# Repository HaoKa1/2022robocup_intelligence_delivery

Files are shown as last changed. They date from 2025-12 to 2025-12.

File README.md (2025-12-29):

# 前言
22年赛道第一次设立，通宵达旦干了两个月，最后获得了冠军，三年过去了，忽然找到留存的资料，想起有好几个赛事群内的群友问我要过资料。虽赛事要求已发生了变化，但基本功能和逻辑一致，于是想直接开源出来，希望能帮助到参赛的同学，也希望赛事能得到更好的发展！  
时间久远，有些文件可能会有错误，欢迎指正，如果内容对你有用的话，请给个小星星⭐️！
# 介绍
PCB硬件设计部分由[@HaoKa1](https://github.com/HaoKa1)完成  
STM32控制代码部分由[@HaoKa1](https://github.com/HaoKa1)/Kaicheng Jin共同完成  
建模由[@hallice](https://github.com/hallice)/[@cdwisaxiaobai](https://github.com/cdwisaxiaobai)共同完成  
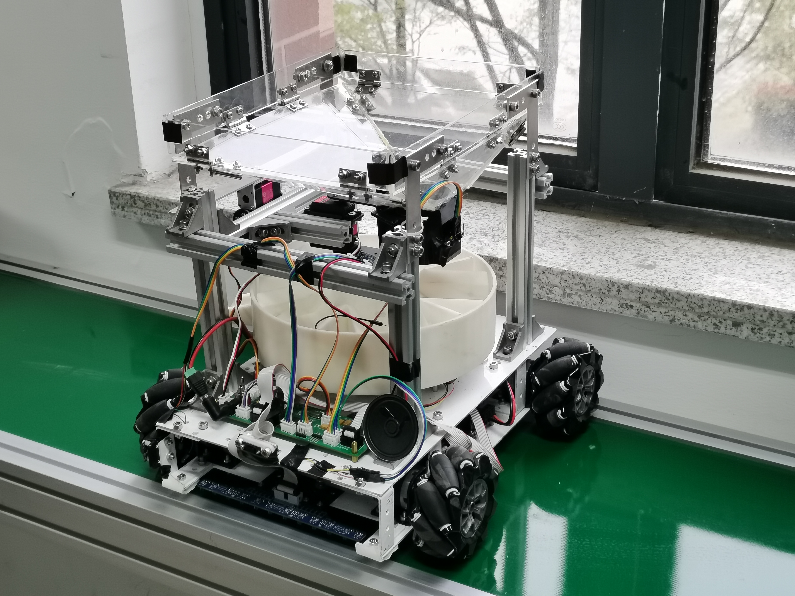
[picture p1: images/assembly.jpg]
Assembly Image

## 建模
结构使用亚克力板、铝合金板材和铝型材搭建，参考models目录下的文件
## 硬件
主控芯片选型为STM32F103RCT6，PCB元器件选型参考hardware目录下的工程文件，外设元器件参考如下，其中因主控芯片定时器数量限制，超声波测距实际上并未被使用                 
### 📡 传感模块
| 传感器类型 | 型号 | 功能 |
|:---|:-----|:-----|
| 激光测距 | ATK-MS53L0M | 距离判断 |
| 超声波测距 | HC-SR04 | 测量距离 |
| 灰度传感器 | 得科技术 | 循迹检测 |
| 颜色识别 | TCS3472XFN | 高尔夫球颜色识别 |

### 🚀 动力模块
| 部件类型 | 型号 | 功能 |
|:---|:-----|:-----|
| 电机驱动 | 得科技术 | 控制电机 |
| 电机 | 任意 | 驱动麦轮 |
| 麦轮 | 任意 | / |
| 舵机 | DS3220/DS3230 | 拨盘、转盘、开门 |

### 🎛️ 其他模块
| 模块类型 | 型号 | 功能 |
|:---|:-----|:-----|
| 扫码模块 | MG65 | 识别二维码 |
| 语音播报模块 | SYN 6288 | 播报信息 |

## 软件
单片机移植FreeRTOS做状态调度，简化调度逻辑，具体流程如下
```mermaid
graph TD
    %% 初始化部分
    Servo_Rest["Servo Rest()<br/>优先级: 2"] -->|挂起相关任务| Start["Start()<br/>优先级: 2"]
    Start -->|判断出发区| GoLine["GoLine()<br/>优先级: 1"]
    
    %% 主巡线循环
    GoLine -->|巡线中| TOF["TOF()<br/>优先级: 2"]
    GoLine -->|转弯信号| Corner["Corner()<br/>优先级: 2"]
    GoLine -->|接收测距通知| Stop["Stop()<br/>优先级: 1"]
    GoLine -->|超声波信号| Wave["Wave()<br/>优先级: 1"]
    
    %% 分选系统（优先级1）
    subgraph "分选系统 - 优先级1"
        Drop["Drop()<br/>1. 接受Stop信号<br/>2. 接受Judge/Select信号<br/>3. 转动<br/>4. 信号给Recognition"]
        Recognition["Recognition()<br/>1. 接受Drop信号<br/>2. 颜色存入队列HC<br/>3. 信号给Judge"]
        Judge["Judge()<br/>1. 接受Recognition信号<br/>2. 颜色判断<br/>3. 无球→JudgetoDrop<br/>4. 有球→颜色存入Index<br/>5. 信号给Select"]
        Select["Select()<br/>1. 接受Judge信号<br/>2. 从Index取颜色<br/>3. 转到对应位置<br/>4. 信号给Drop"]
        
        Drop -->|信号量D| Recognition
        Recognition -->|信号量Recognition| Judge
        Judge -->|无球: JudgetoDrop| Drop
        Judge -->|有球: 存入队列Index| Select
        Select -->|SelecttoDrop| Drop
    end
    
    %% 避障系统
    Wave -->|距离<250| Avoid["Avoid()<br/>优先级: 2"]
    Wave -->|>=250| GoLine
    Avoid -->|结束条件| GoLine
    
    %% 停车处理流程
    TOF -->|测距数据| Stop
    Stop -->|第一次停车| GoLineLow["挂起Goline<br/>拉起GolineLow"]
    Stop -->|通知Drop| Drop_Start["分选开始"]
    Stop -->|第2-7次停车| Movein["Movein()<br/>优先级: 1"]
    Stop -->|第8次停车| SlowCross["减速过跷跷板"]
    
    %% 货站操作流程
    Movein -->|右侧平移| QR["QR()<br/>优先级: 2"]
    QR -->|数据=0| Speak_0["Speak()<br/>播报0<br/>优先级: 3"]
    QR -->|数据≠0| Put["Put()<br/>优先级: 1"]
    
    QR -->|QRtoMoveout| Moveout["Moveout()<br/>优先级: 1"]
    Speak_0 -->|播报完成| Moveout
    Put -->|PuttoSpeak| Speak_1["Speak()<br/>播报颜色<br/>优先级: 3"]
    Put -->|PuttoMoveout| Moveout
    Speak_1 -->|播报完成| Moveout
    
    %% 继续前进
    Moveout -->|MoveouttoForward| Forward["Forward()<br/>优先级: 1"]
    Stop -->|20秒后| Forward_Continue["拉起Goline/相关任务"]
    Forward -->|拉起TOF/Goline/Stop/QR| GoLine
    
    %% 特殊流程
    Stop -->|第7次后| EnableFrontTOF["开启前方测距"]
    Corner -->|第4次转弯| ReturnStart["返回出发区"]
    
    %% 结束条件
    Judge -->|10个球分选完| DeleteModules["删除Drop/Recognition/Judge/Select"]
    ReturnStart --> End["流程结束"]

    %% 样式定义
    classDef priority1 fill:#e1f5fe,stroke:#0288d1,stroke-width:2px
    classDef priority2 fill:#f3e5f5,stroke:#7b1fa2,stroke-width:2px
    classDef priority3 fill:#e8f5e8,stroke:#2e7d32,stroke-width:2px
    classDef special fill:#fff3e0,stroke:#ef6c00,stroke-width:2px
    
    class Drop,Recognition,Judge,Select,GoLine,Stop,Movein,Put,Moveout,Forward,Wave priority1
    class Servo_Rest,Start,Corner,TOF,QR,Avoid priority2
    class Speak_0,Speak_1 priority3
    class DeleteModules,ReturnStart,EnableFrontTOF,SlowCross special
```

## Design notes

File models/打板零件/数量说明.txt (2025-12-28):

漏斗——1个
底板钣金——1个
横梁钣金——1个
底盘上板——1个
激光测距——2个
底盘_筛分连接——3个
镜像底盘_筛分连接——3个
平面直角连接——4个
转盘固定——4个

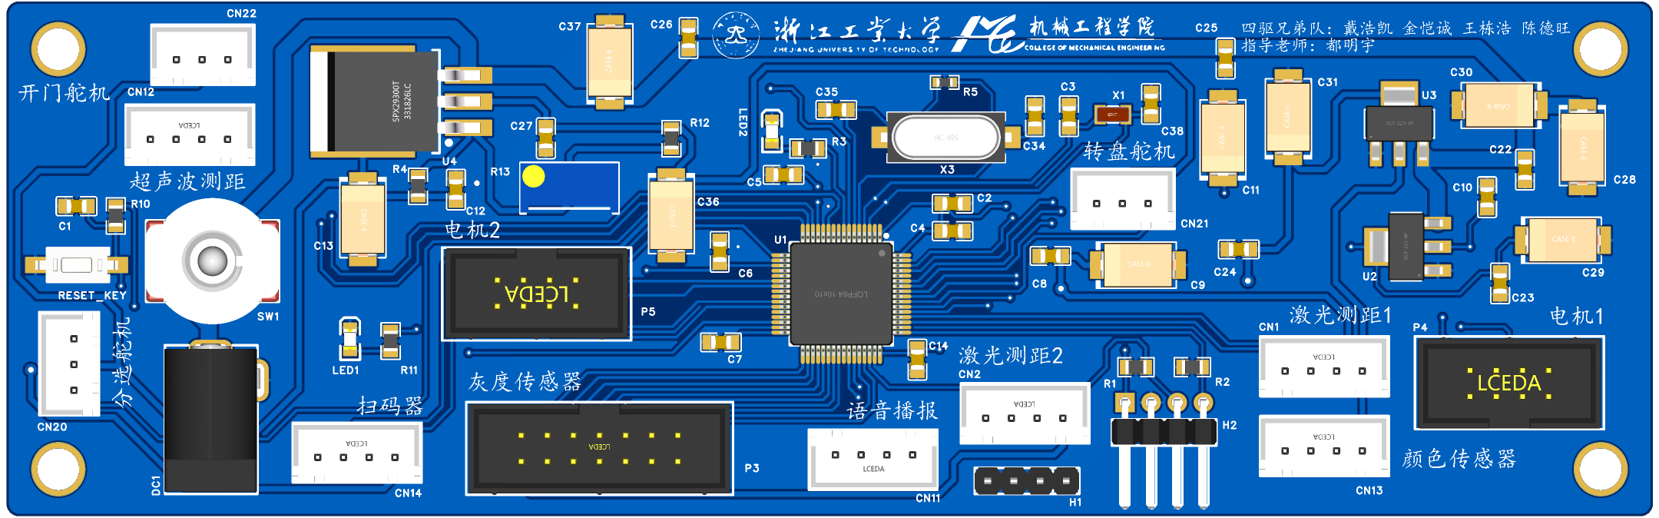
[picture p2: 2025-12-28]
hardware/3D_PCB.png

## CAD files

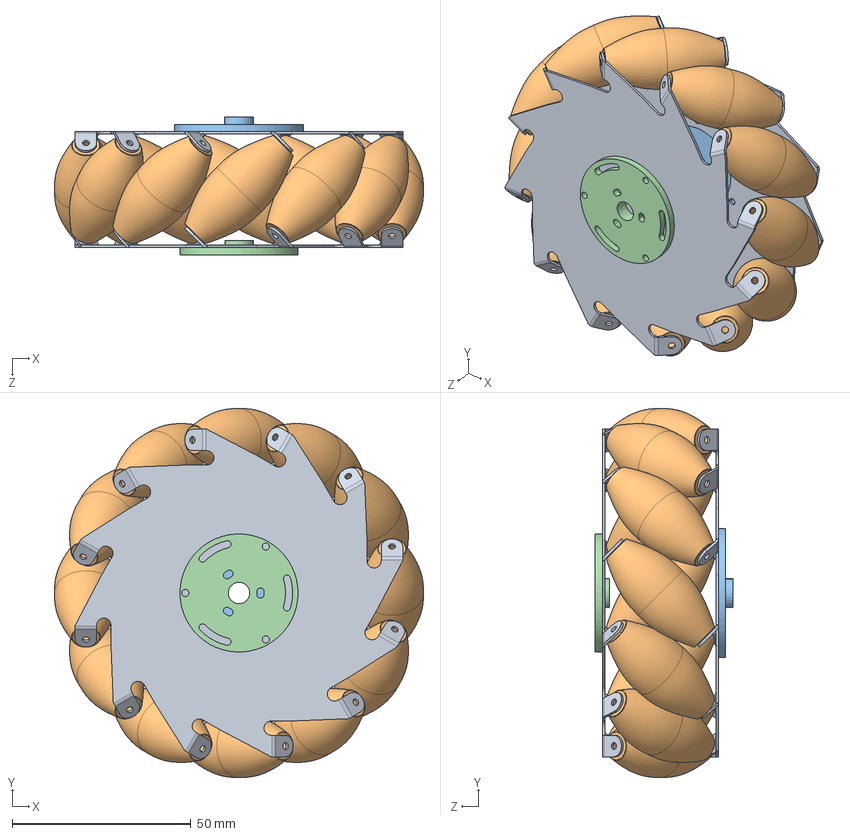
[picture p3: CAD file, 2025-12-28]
models/麦轮/麦轮.SLDASM
103.1 x 103.1 x 38.5 mm
麦轮轮毂 x 2
麦轮麦粒 x 12
轮毂配件
轮毂配件外

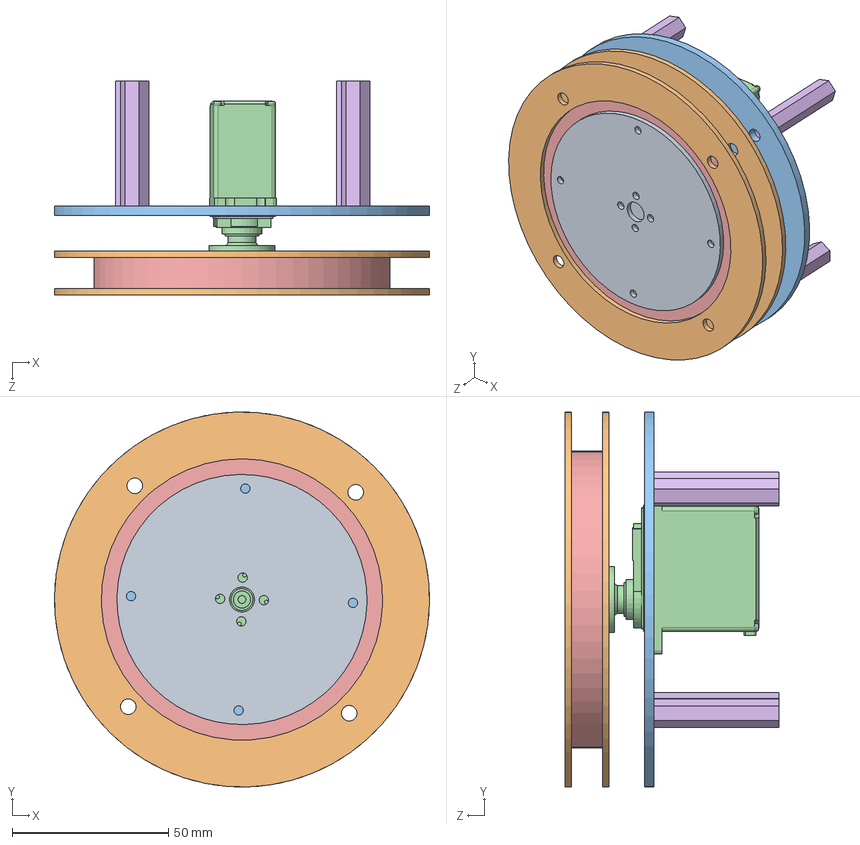
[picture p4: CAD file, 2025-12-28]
models/转盘/转盘.SLDASM
120.0 x 119.9 x 68.4 mm
上板 x 2
转盘轴承夹板 x 2
转盘底板
儋州舵机
轴承
铜柱 x 4

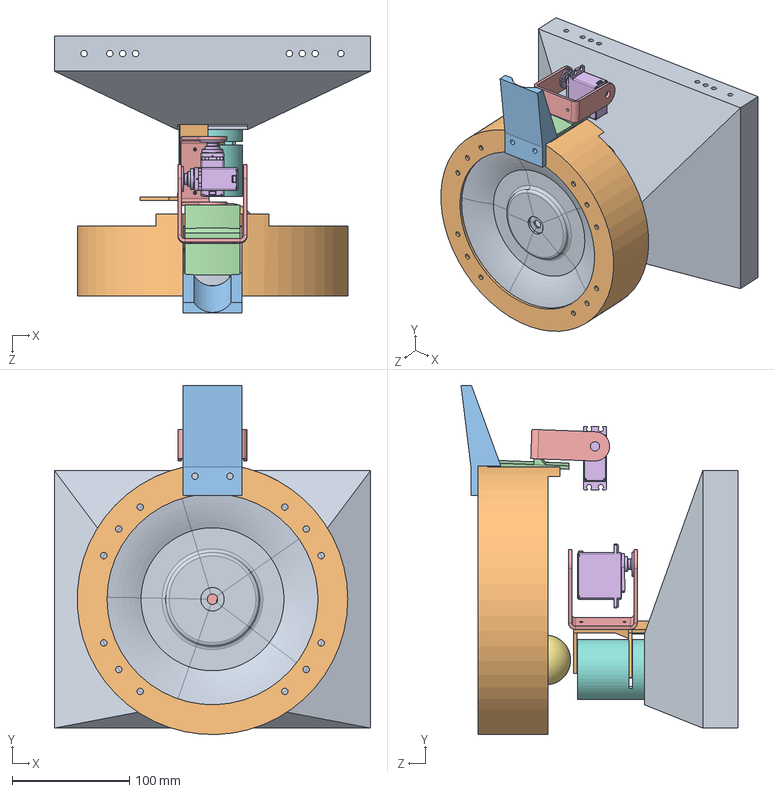
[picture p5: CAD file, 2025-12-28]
models/储存模块2.0/装配体2.SLDASM
270.0 x 297.9 x 236.5 mm
筛选器 x 5
遮挡
滑槽
挡板1
舵机架 x 2
儋州舵机 x 2
高尔夫球 x 4
圆筒
漏斗
遮挡转轴

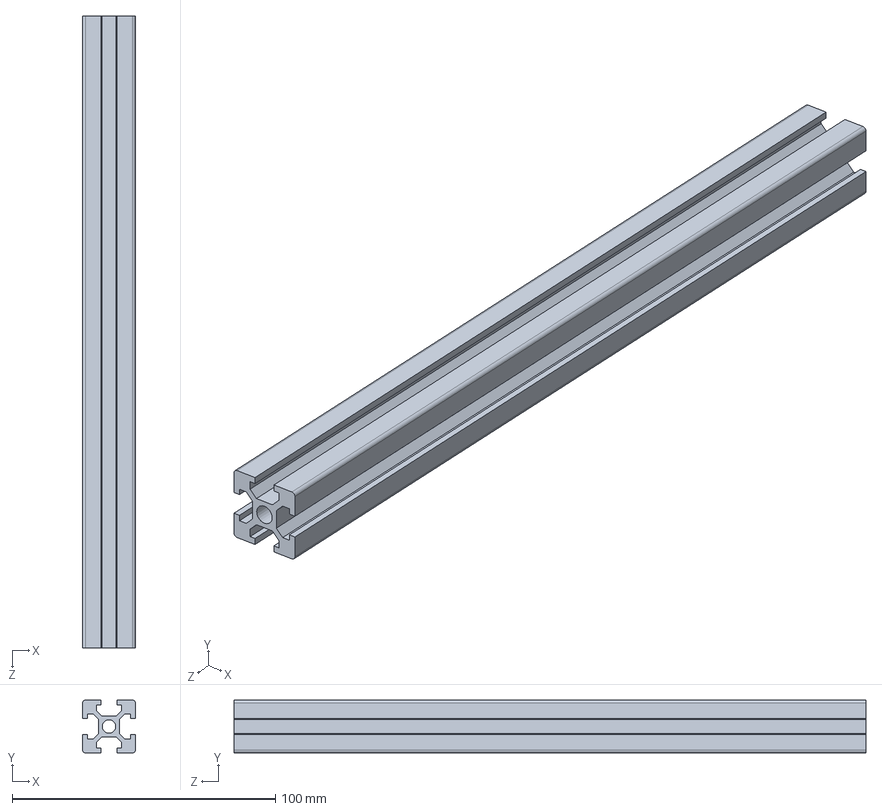
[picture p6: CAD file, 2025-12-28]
models/储存模块2.0/铝型材_20x240_li.SLDPRT
20.0 x 20.0 x 240.0 mm

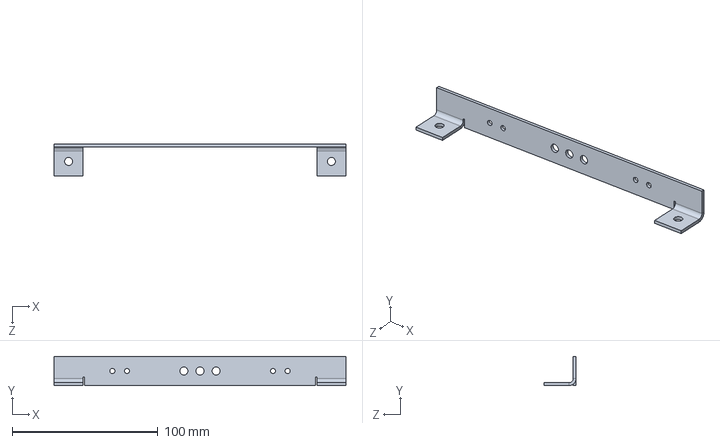
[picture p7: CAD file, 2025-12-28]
models/打板零件/横梁钣金.SLDPRT
200.0 x 20.0 x 22.0 mm

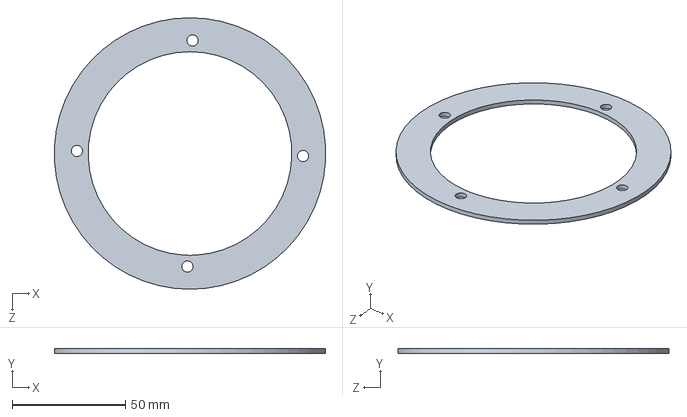
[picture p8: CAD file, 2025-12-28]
models/转盘/转盘轴承夹板.SLDPRT
119.8 x 2.00 x 120.0 mm

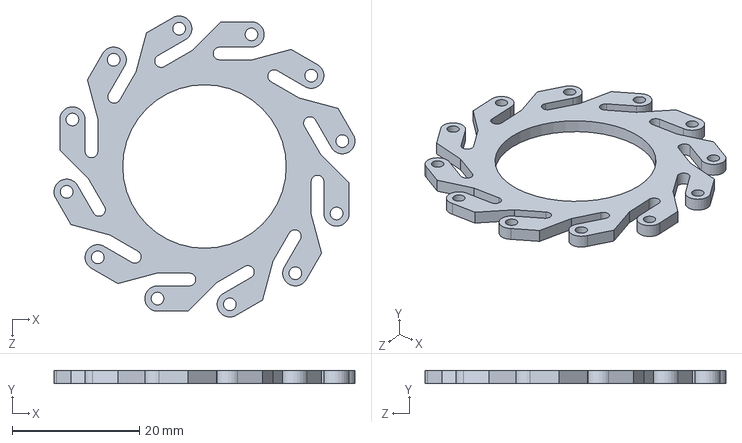
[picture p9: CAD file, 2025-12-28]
models/轮毂小.SLDPRT
47.2 x 2.00 x 47.2 mm

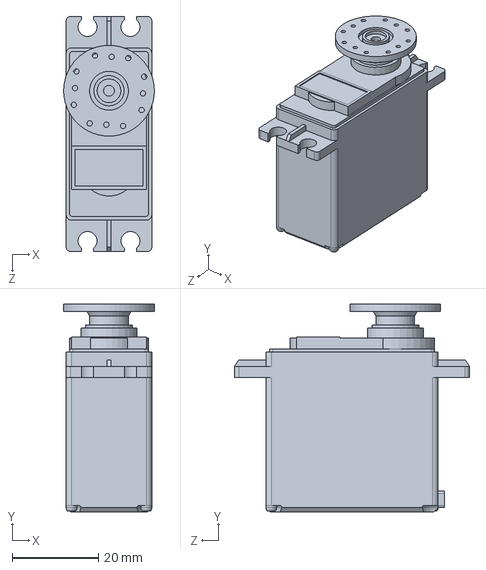
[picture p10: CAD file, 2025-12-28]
models/储存模块2.0/儋州舵机.SLDPRT
21.0 x 48.1 x 54.4 mm

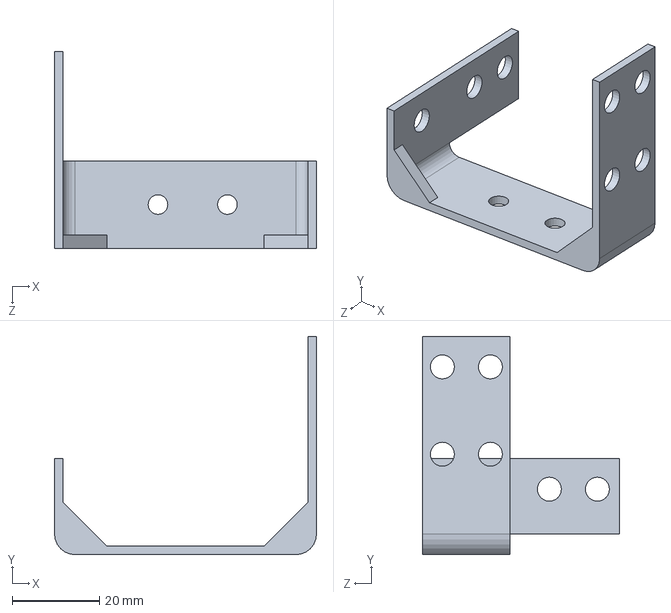
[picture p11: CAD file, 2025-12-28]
models/打板零件/镜向底盘_筛分连接.SLDPRT
60.0 x 50.0 x 45.0 mm

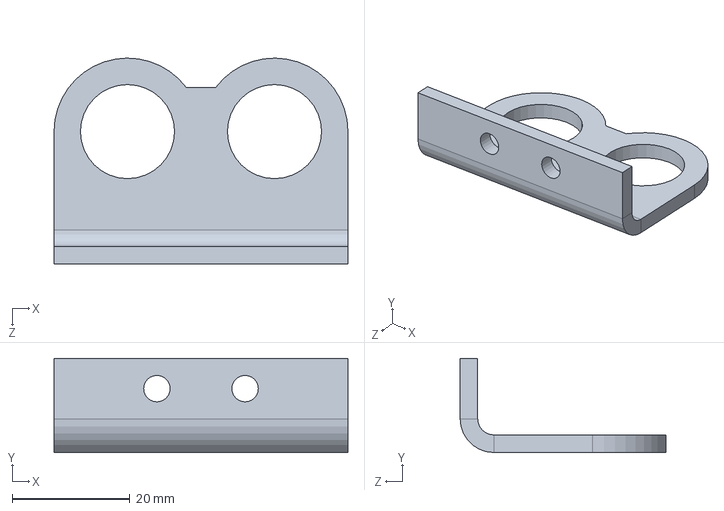
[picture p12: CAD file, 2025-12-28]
models/超声波测距基座.SLDPRT
50.0 x 16.0 x 35.0 mm

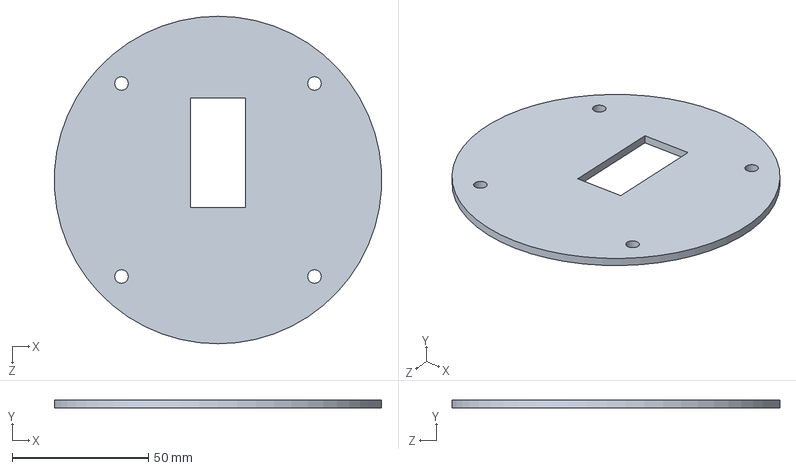
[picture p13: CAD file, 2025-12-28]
models/转盘/转盘底板.SLDPRT
119.8 x 3.00 x 120.0 mm

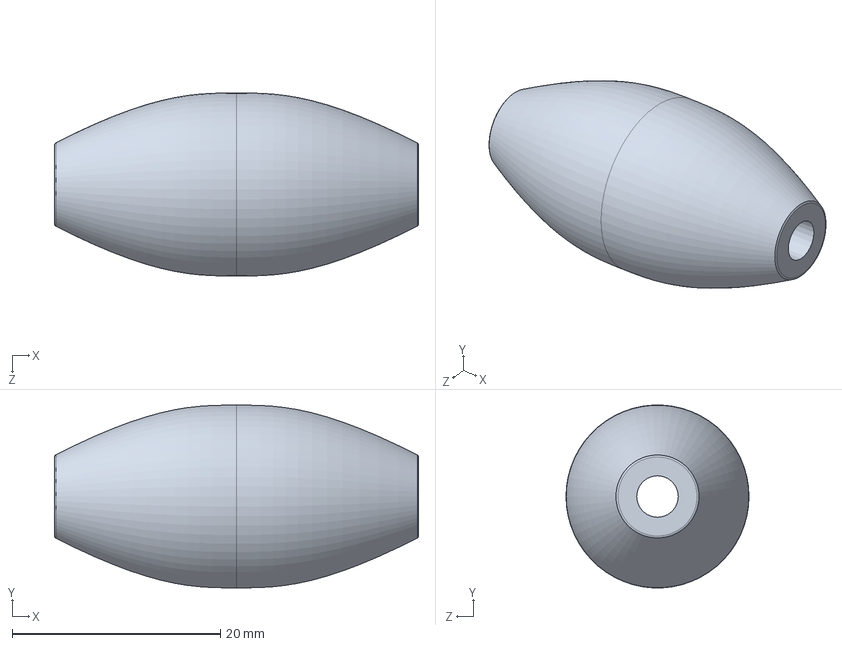
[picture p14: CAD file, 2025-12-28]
models/麦轮/麦轮麦粒.SLDPRT
35.0 x 17.6 x 17.6 mm

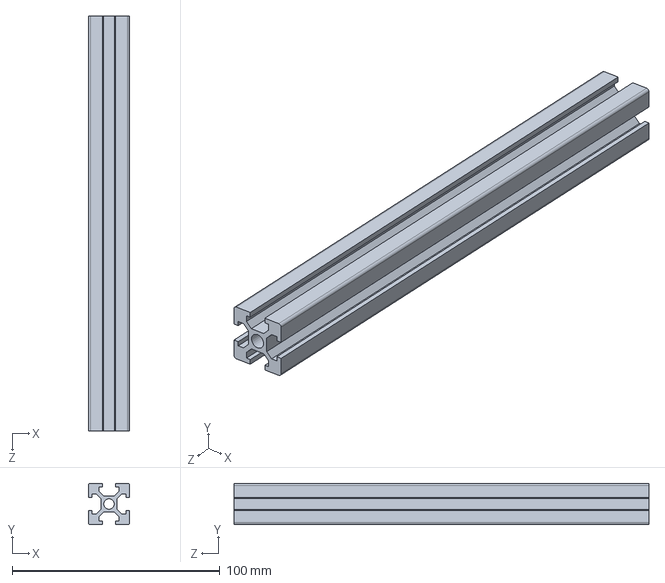
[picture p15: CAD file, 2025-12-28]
models/储存模块2.0/铝型材_20x200_shang.SLDPRT
20.0 x 20.0 x 200.0 mm

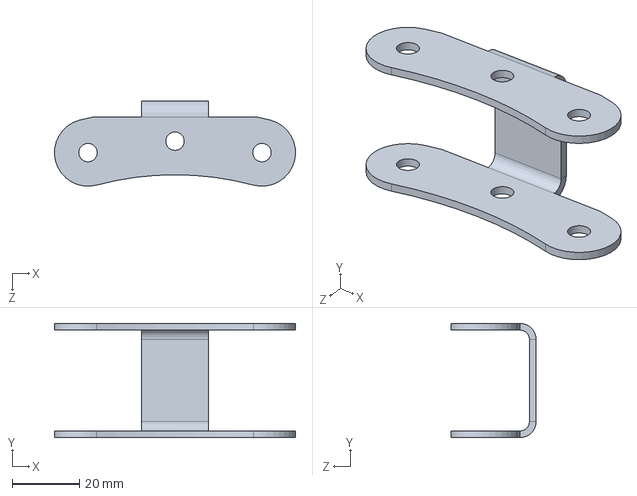
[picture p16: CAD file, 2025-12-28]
models/打板零件/转盘固定.SLDPRT
71.7 x 34.0 x 25.4 mm

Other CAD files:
models/总装.SLDASM
models/转盘/上板.SLDPRT
models/镜向底盘_筛分连接.SLDPRT
models/麦轮/37电机支架.SLDPRT
models/siquxiongdi_PCB.SLDPRT
models/stm32f3c.SLDPRT
models/储存模块2.0/圆筒.SLDPRT
models/储存模块2.0/导管.SLDPRT
models/储存模块2.0/平面直角连接架.SLDPRT
models/储存模块2.0/挡板1.SLDPRT
models/储存模块2.0/横梁钣金.SLDPRT
models/储存模块2.0/滑槽.SLDPRT
models/储存模块2.0/漏斗.SLDPRT
models/储存模块2.0/漏斗改.SLDPRT
models/储存模块2.0/筛选器.SLDPRT
models/储存模块2.0/筛选器全.SLDPRT
models/储存模块2.0/舵机架.SLDPRT
models/储存模块2.0/转轴.SLDPRT
models/储存模块2.0/遮挡.SLDPRT
models/储存模块2.0/遮挡转轴.SLDPRT
models/储存模块2.0/铝型材_20x110.SLDPRT
models/储存模块2.0/铝型材_20x180.SLDPRT
models/储存模块2.0/铝型材_20x200_li.SLDPRT
models/储存模块2.0/高尔夫球.SLDPRT
models/大稳压.SLDPRT
models/寻迹电路板.SLDPRT
models/小稳压.SLDPRT
models/底板钣金.SLDPRT
models/底盘_筛分连接.SLDPRT
models/底盘上板.SLDPRT
models/强化连接底板.SLDPRT
models/循迹模块固定板.SLDPRT
models/打板零件/平面直角连接架.SLDPRT
models/打板零件/底板钣金.SLDPRT
models/打板零件/底盘_筛分连接.SLDPRT
models/打板零件/底盘上板.SLDPRT
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

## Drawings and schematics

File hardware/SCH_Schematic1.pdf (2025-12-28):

## 高频和低频晶振

# 3.3V稳压

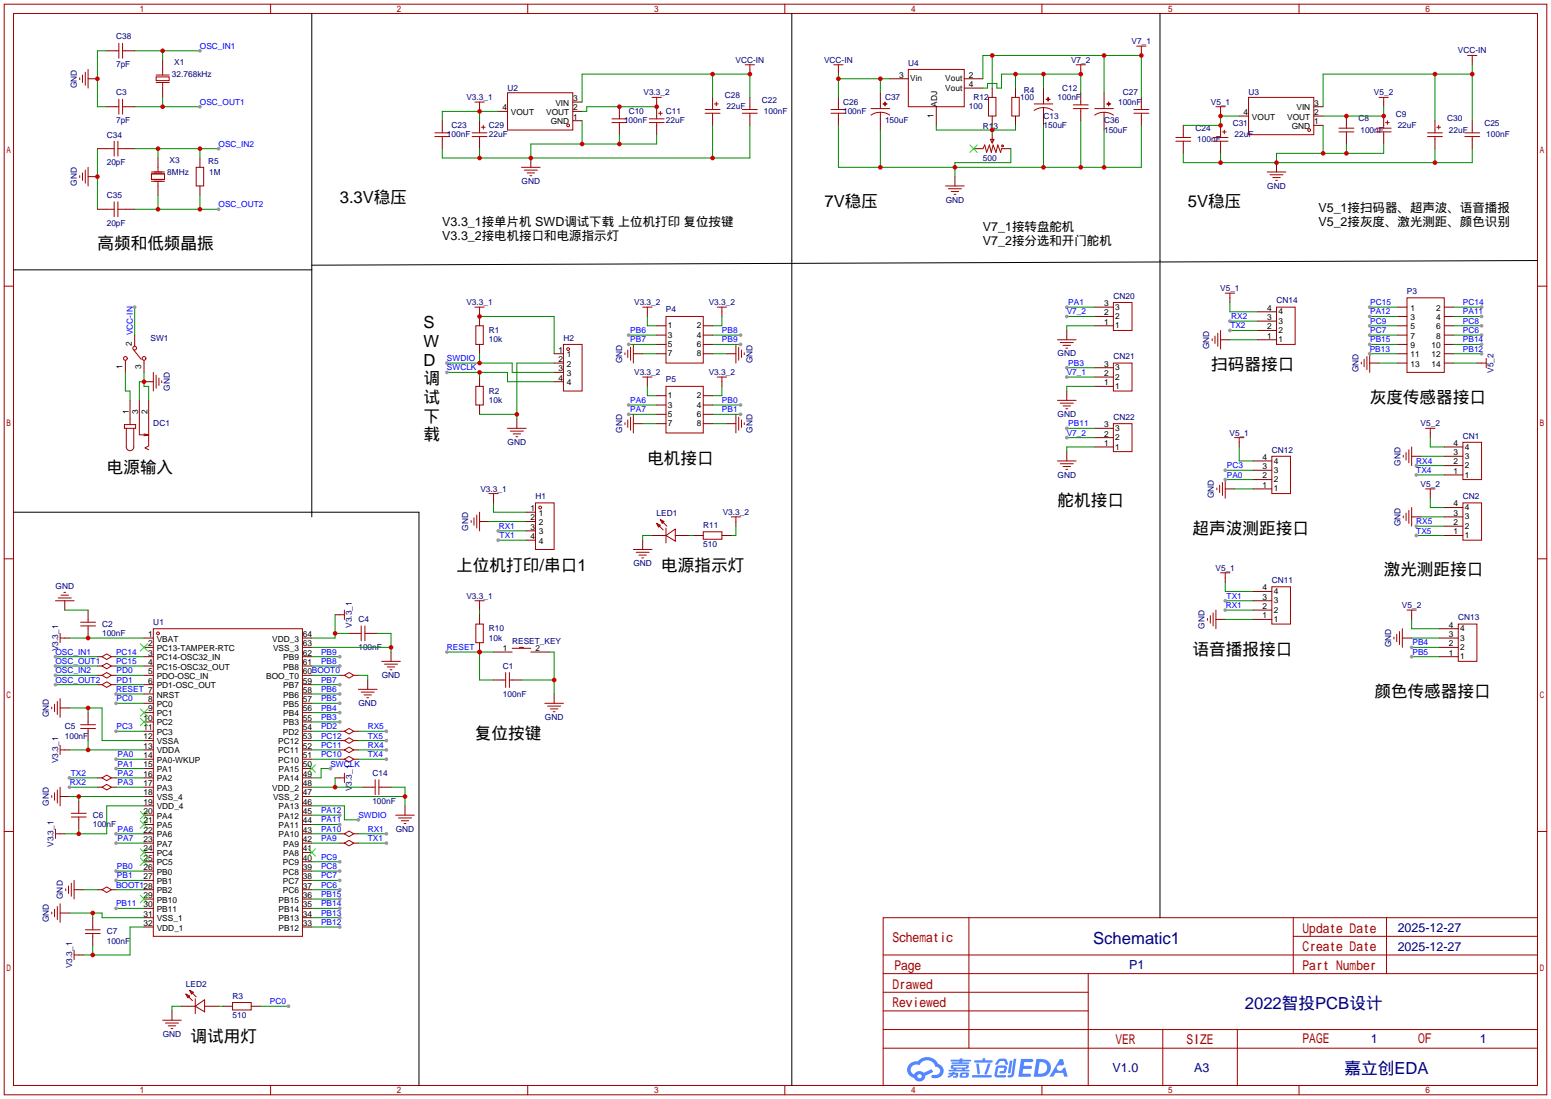
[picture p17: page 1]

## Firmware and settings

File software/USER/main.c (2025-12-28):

/*
*---------------------------------中国机器人大赛智能投送赛道国赛---------------------------------*
芯片型号：STM32F103RCT6
硬件型号：
	灰度传感器：S312B--模拟量版本（数字量版本将导致红蓝出发区出发严重问题，需长时间调试，互换性不强，不建议使用）
	颜色识别模块：TCS34725
	激光测距模块：正点原子MS53L0M（此版本为标注量程为2m，超出量程将随机返回错误数值，易产生问题，建议上4m版本的MS53L1M）
	超声波测距模块：HC-SR04（超声波的优势在于无需使用串口，我们选用的芯片型号IO口过少，使用十分紧张，
	因此在避障时设计采用超声波，减少对串口的占用，但因为超声波的trig需要TIM发出PWM波信号，而这个信号又会与电机驱动的PWM输出产生冲突，
	因此我们最终两害相权取其轻，放弃了超声波测距的使用，但对于一个扇形的测距范围和一个IO紧张的设计来说，可以尝试攻克这个PWM的冲突问题以更好发挥性能
	电机驱动：得科技术2路大功率驱动
		（1、建议电机驱动队伍重新购买其他硬件或自行设计，此驱动200一块，性价比太低，此外MOS管虚焊，短路等问题频繁
			2、选购驱动时可选择较便宜硬件，此赛项赛道短，调整时间少，运动速度慢，无需大功率驱动支持）				
	数字舵机：RDS3218（舵机型号无需过于拘泥，但必须是数字舵机，180度舵机选择15kg扭矩，360度舵机选择30kg扭矩即可）
	扫码模块：GM65	
	语音播报模块：SYN6288	
	减速电机：不再建议使用减速电机，在启动和急停时十分不稳定，并且各个电机的电气特性存在差异，需要在软件上不断调整，可采用编码电机等，
	但对于驱动部分的代码则需自行修改，另外选购时转速100转完全满足要求，过高转速反而影响减速比参数
选购指南：如果赛事场地大小、规则等没有大的变动，硬件可完全参照以上购买，如赛事有其他要求，在选购时，建议大家选择大店铺购买，如正点原子等，
	价格可能略贵，但是在例程代码和技术支持和售后服务上都有较好的保障，能让大家快速上手调试，其他例如risym之流的淘宝店铺，
	完全没有技术支持，只能凭论坛发问和自行摸索，会花费大量时间
操作系统：FreeRTOS
开发成员：Haokai Dai/Kaicheng Jin
指导教师：Mingyu Du
注释维护：Haokai Dai
更新时间：2025/12/08
*---------------------------------中国机器人大赛智能投送赛道国赛---------------------------------*
*/
#include "stm32f10x.h"
#include "led.h"
#include "GreyScale.h"
#include "Laser.h"
#include "Motor.h"
#include "Route.h"
#include "syn6288.h"
#include "Servo.h"
#include "delay.h"
#include "sys.h"
#include "usart.h"
#include "USART1.h"
#include "USART2.h"
#include "uart4.h"
#include "uart5.h"
#include "tcs34725.h"
#include "color.h"
#include "FreeRTOS.h"
#include "task.h"
#include "semphr.h"
/**************SYN6288芯片设置命令（模块配置，无需改动）*********************/
u8 SYN_StopCom[] = {0xFD, 0X00, 0X02, 0X02, 0XFD}; //停止合成
u8 SYN_SuspendCom[] = {0XFD, 0X00, 0X02, 0X03, 0XFC}; //暂停合成
u8 SYN_RecoverCom[] = {0XFD, 0X00, 0X02, 0X04, 0XFB}; //恢复合成
u8 SYN_ChackCom[] = {0XFD, 0X00, 0X02, 0X21, 0XDE}; //状态查询
u8 SYN_PowerDownCom[] = {0XFD, 0X00, 0X02, 0X88, 0X77}; //进入POWER DOWN 状态命令


/*
*******定义一个转盘位置与相应颜色的结构体**********
index为颜色代表的数字1-5
quantity为某位置中index颜色已有球的数量
*/
typedef struct{
	unsigned short index; 
	unsigned short quantity;
}POSITION;
POSITION position[5]={0,0};
/*	
***************************************测距模块********************************
注意：上位机通过USB-TTL模块连接开发板的串口1，可以用串口调试助手查看测距结果
测距模块A接在开发板串口4（PC10、PC11），串口4测距结果始终保存在A_distance变量中
测距模块B接在开发板串口5（PC12、PD2），串口5测距结果始终保存在B_distance变量中
*/
extern uint16_t A_distance,B_distance;
/*
***********************************操作系统说明****************************************
代码采用的是FreeRTOS操作系统，本工程已经将操作系统移植，与操作系统相关的代码均在main函数中，
涉及到的任务时间片轮转、句柄、队列、任务调度、优先级等知识需先行了解学习，
通过OS，可以让单片机实现伪多线程的功能，在22年的比赛中，规则中的“边走边分选”要求需要OS
，比赛时将此规则弱化了，但我认为使用OS能够更好地理清思路和逻辑，也方便后续的代码维护
*/
//各任务句柄
TaskHandle_t 	Drop_Handle;
TaskHandle_t	Recognition_Handle;
TaskHandle_t	Judge_Handle;
TaskHandle_t	Select_Handle;
TaskHandle_t 	Stop_Handle;
TaskHandle_t 	Movein_Handle;
TaskHandle_t 	QR_Handle;
TaskHandle_t 	Put_Handle;
TaskHandle_t 	Moveout_Handle;
TaskHandle_t 	Forward_Handle;
TaskHandle_t  Speak_Handle;
TaskHandle_t	Wave_Handle;
TaskHandle_t	Avoid_Handle;
TaskHandle_t	TOF_Handle;
TaskHandle_t	Goline_Handle;
TaskHandle_t	Corner_Handle;
TaskHandle_t	GolineLow_Handle;
TaskHandle_t	GoLineNew_Handle;
TaskHandle_t	Gohome_Handle;

//各任务所需队列
QueueHandle_t	xQueueHC;
QueueHandle_t	xQueueIndex;
QueueHandle_t	xQueueTOF;
QueueHandle_t	xQueueQR;
QueueHandle_t	xQueueSpeak;

/*
RTOS移植所需函数，无需修改
*/
static void prvSetupHardware( void ){
	/* Start with the clocks in their expected state. */
	RCC_DeInit();

	/* Enable HSE (high speed external clock). */
	RCC_HSEConfig( RCC_HSE_ON );

	/* Wait till HSE is ready. */
	while( RCC_GetFlagStatus( RCC_FLAG_HSERDY ) == RESET )
	{
	}

	/* 2 wait states required on the flash. */
	*( ( unsigned long * ) 0x40022000 ) = 0x02;

	/* HCLK = SYSCLK */
	RCC_HCLKConfig( RCC_SYSCLK_Div1 );

	/* PCLK2 = HCLK */
	RCC_PCLK2Config( RCC_HCLK_Div1 );

	/* PCLK1 = HCLK/2 */
	RCC_PCLK1Config( RCC_HCLK_Div2 );

	/* PLLCLK = 8MHz * 9 = 72 MHz. */
	RCC_PLLConfig( RCC_PLLSource_HSE_Div1, RCC_PLLMul_9 );

	/* Enable PLL. */
	RCC_PLLCmd( ENABLE );

	/* Wait till PLL is ready. */
	while(RCC_GetFlagStatus(RCC_FLAG_PLLRDY) == RESET)
	{
	}

	/* Select PLL as system clock source. */
	RCC_SYSCLKConfig( RCC_SYSCLKSource_PLLCLK );

	/* Wait till PLL is used as system clock source. */
	while( RCC_GetSYSCLKSource() != 0x08 )
	{
	}

	/* Enable GPIOA, GPIOB, GPIOC, GPIOD, GPIOE and AFIO clocks */
	RCC_APB2PeriphClockCmd(	RCC_APB2Periph_GPIOA | RCC_APB2Periph_GPIOB |RCC_APB2Periph_GPIOC
							| RCC_APB2Periph_GPIOD | RCC_APB2Periph_GPIOE | RCC_APB2Periph_AFIO, ENABLE );

	/* SPI2 Periph clock enable */
	RCC_APB1PeriphClockCmd( RCC_APB1Periph_SPI2, ENABLE );


	/* Set the Vector Table base address at 0x08000000 */
	NVIC_SetVectorTable( NVIC_VectTab_FLASH, 0x0 );

	NVIC_PriorityGroupConfig( NVIC_PriorityGroup_4 );

	/* Configure HCLK clock as SysTick clock source. */
	SysTick_CLKSourceConfig( SysTick_CLKSource_HCLK );
}

/*
**************舵机复位****************
将三个舵机复位并临时挂起不使用的子任务
*/
void RervoReset_task(void *pvParameters){
	Color_Reset();
	vTaskDelay(10);
	vTaskSuspend(GoLineNew_Handle);
	vTaskSuspend(Movein_Handle);
	vTaskSuspend(Moveout_Handle);
	vTaskSuspend(QR_Handle);
	vTaskSuspend(Put_Handle);
	vTaskSuspend(Avoid_Handle);
	vTaskSuspend(Speak_Handle);
	vTaskSuspend(GolineLow_Handle);
	vTaskSuspend(Wave_Handle);
	vTaskDelete(NULL);
}
/*
***********************************出发区出发*************************************
从红/蓝色出发区出发，灰度第7路为0并且第八路为1时判断为已走到赛道中心，结束出发区任务
*/
void Start_task(void *pvParameters){
	Route_Start();
	while(1){
		if(GREY_7==0&&GREY_8==1)	break;
	}

	vTaskDelete(NULL);
}
/*
********************************侧边激光测距***************************************
获得串口返回的B_distance数值，并判断是否在范围内，如果cnt==1，那么是第一次侧边有箱体
（即翻斗）立即发信号给停车子任务，如果cnt!=1，那么是碰到了后续需要投球的货站，则继续前进，
直到B_distance数值超出范围，认为小车移动到了箱体正中央，发信号给停车
注：B_distance的阈值范围和安装位置有关，与场地布置也有关，需要自行测试确定
*/
void TOF_task(void *pvParameters){
	TickType_t xLastWakeTime;
	uint16_t Send_distance;
	uint8_t	cnt=0;
	while(1){
		Send_distance=B_distance;
		if((Send_distance>=90&&Send_distance<=220)){
			cnt++;
			if(cnt==1){
				xTaskNotifyGive(Stop_Handle);
				vTaskSuspend(Goline_Handle);
				vTaskSuspend(NULL);			
			}
			else{
				while(1){
					if(B_distance>=220)	break;
				}
				xTaskNotifyGive(Stop_Handle);
				vTaskSuspend(Goline_Handle);
				vTaskSuspend(NULL);				
			}

		}
		xLastWakeTime = xTaskGetTickCount();
		vTaskDelayUntil(&xLastWakeTime,20);		
	}
}
/*
**************前方激光测距**************
采用的是激光测距模块，有能力可改用超声波
*/
void Wave_task(void *pvParameters){
	TickType_t xLastWakeTime;
	while(1){
		if(330>=A_distance&&A_distance>=280){
			vTaskSuspend(Goline_Handle);
			xTaskNotifyGive(Avoid_Handle);
			vTaskSuspend(NULL);
		}
		xLastWakeTime = xTaskGetTickCount();
		vTaskDelayUntil(&xLastWakeTime,10);
	}
}
/*
***********转盘转动下球*************
调用Color_Drop
*/
void Drop_task(void *pvParameters){
	uint16_t val=0;
	while(1){
		val=ulTaskNotifyTake(pdTRUE,2);
		if(val){
				Color_Drop();
				vTaskDelay(5);
				xTaskNotifyGive(Recognition_Handle);	//将信号发给Recognition
		}
	}

}
/*
*******************************颜色识别************************************
启动颜色识别模块的TCS34725的IIC传输，识别两次是为了防止当求还没落下来时误判了球的颜色，
如果两次值差别较大，则重新识别一次，否则取两次的平均值
实际上可以只判断一次，因为模块识别十分精确，如需提升速度可以省略二次识别
*/
void Recognition_task(void *pvParameters){
	uint16_t val=0;
	HC Get1_hc,Get2_hc,Send_hc;
	TCS34725_I2C_Start();
	while(1){
		val=ulTaskNotifyTake(pdTRUE,2);
		if(val){
			vTaskDelay(20);
			Get1_hc=Color_recognition();
			vTaskDelay(10);
			Get2_hc=Color_recognition();
			vTaskDelay(5);
			if(Get1_hc.h-Get2_hc.h>15||Get2_hc.h-Get1_hc.h>15){
				Send_hc=Color_recognition();
			}
			else{
				Send_hc.h=(Get1_hc.h+Get2_hc.h)/2;
				Send_hc.c=(Get1_hc.c+Get2_hc.c)/2;
			}
			xQueueSendToBack(xQueueHC,&Send_hc,pdMS_TO_TICKS(5));
			xTaskNotifyGive(Judge_Handle);

		}
	}
}
/*
****************************颜色索引判断**********************
调用Send_Judge，通过传来的颜色数值判断球对应的是1-5哪个数字
*/
void Judge_task(void *pvParameters){
	uint16_t val=0;
	uint16_t Send_judge;
	HC Receive_hc;
	while(1){
		val=ulTaskNotifyTake(pdTRUE,2);
		if(val){
			xQueueReceive(xQueueHC,&Receive_hc,pdMS_TO_TICKS(5));//从队列里读取数据
			Send_judge=Color_Judge(Receive_hc);
			xQueueSendToBack(xQueueIndex,&Send_judge,pdMS_TO_TICKS(5));//把颜色序号信息送入队列
			xTaskNotifyGive(Select_Handle);
		}
	}
}
/*
**************************************颜色分选********************************************
如果收到的Judge信号非0，那么判断到了通道内确实有球需要分选，否则即为此次通道内无求，
若无球则需重新执行下落等一系列子任务。
若有球，先判断Judge信号是否与position中的index值有对应，如果有对应的，则之前这个颜色
的球已经落下过，在转盘中已经有它对应的位置，那么把这个球也投到这个位置，并且quantity++
（在代码中，quantity实际并没有使用到，可以将它作为同一颜色的球是否都已经完全落下的辅助判断）
如果没有对应的index值，说明这个球是一个“新球”，需要找一个离初始位置最近的新位置来放置这个球

current和past两个变量记录的是现在所在的转盘位置和上次放球的转盘位置，做差值即可计算
转动延时时间，545这个值是安装后测试的舵机初始位置，建议后续使用时将其宏定义，否则改动较麻烦
*/
void Select_task(void *pvParameters){
	uint16_t val=0,timer;
	static uint16_t current=0;
	static uint16_t	past=0;
	uint16_t Receive_judge,cnt;
	while(1){
		val=ulTaskNotifyTake(pdTRUE,2);
		if(val){
			xQueueReceive(xQueueIndex,&Receive_judge,pdMS_TO_TICKS(5));//从队列里读取信息
			if(Receive_judge!=0){
				for(cnt=0;cnt<=4;cnt++){
					if(Receive_judge==position[cnt].index) break;
				}
				current=cnt;
				if(cnt<5){
					position[cnt].quantity++;
					TIM_SetCompare2(TIM2,545+cnt*400);
					timer=(current-past>=0)?current-past:past-current;
				}
				else{
					for(cnt=0;cnt<=4;cnt++){
						if(position[cnt].index==0){
							position[cnt].index=Receive_judge;
							position[cnt].quantity++;
							TIM_SetCompare2(TIM2,545+cnt*400);
							timer=(current-past>=0)?current-past:past-current;
							break;
						}
					}
				}
			}
			else{
			}
				vTaskDelay(timer*30+15);
				past=current;
				Color_Drop();
				vTaskDelay(50);
			xTaskNotifyGive(Drop_Handle);
		}
	}
}
/*
************************************巡线*********************************************
if中GREY_1为灰度传感器最左侧第一路，如果第一路为0，那么到了直角转弯的转角，向前移动后，
原地逆时针转动，知道第七路为0，判断转正
else中调用巡线函数进行循迹
*/
void GoLine_task(void *pvParameters){
	while (1)
	{
		if(GREY_1==0){
			Route_Straight();
			vTaskDelay(30);
			Route_Stop();
			vTaskDelay(20);
			while(GREY_7!=0){
				Route_TurnCorner();
			}
		}
		else{
			Route_GoLine();
		}
	}
}
/*
**********************转弯（未使用）*******************
可以将转弯单独分为一个子任务，如果任务切片需要可以采用
void Corner_task(void *pvParameters){
	TickType_t xLastWakeTime;	
	uint16_t val;
	while(1){
		val=ulTaskNotifyTake(pdTRUE,pdMS_TO_TICKS(5));
		if(val){
			Route_Straight();
			xLastWakeTime = xTaskGetTickCount();
			vTaskDelayUntil(&xLastWakeTime,15);
			Route_TurnCorner();	
			xLastWakeTime = xTaskGetTickCount();
			vTaskDelayUntil(&xLastWakeTime,800);		
		}
		xLastWakeTime = xTaskGetTickCount();
		vTaskDelayUntil(&xLastWakeTime,10);
	}
}
*/
/***********模块初始化*************/
void __init__(void){
	NVIC_Configuration();
	delay_init();	//延时函数初始化
	LED_Init();		//LED灯初始化	OK
	Motor_Configure(); 	//电机驱动初始化
	GREY_Configure();		//灰度传感器初始化	OK
	TCS34725_Init();		//颜色识别传感器初始化	OK
	TIM5_PWM_Init(19999,71);		//所有舵机初始化 OK
	TIM2_PWM_Init(19999,71);
	UART4_init(115200);	//左测距波特率
	UART5_init(115200);	//前测距波特率
	USART1_Init(9600);	//语音播报波特率
	usart_init2(9600);	//扫码器波特率	
	GPIO_Config();	//JAGT disable 
	TCS34725_Init();
	UART5_Start();
	USART2_Stop();
	UART4_Stop();
}
/*
**********************************停车*************************************************
第一次停车时，拉起后续需要的子任务，然后进行逐级减速，停车后发送队列信息，进行分球操作
如果是第二次停车，那么可以删除分球的子任务（因为在之前到达第一个货站之前已经全部分选完成）
后续进行平移投球即可
*/
void Stop_task(void *pvParameters){
	uint16_t val;
	static uint16_t	cnt=0;
	while(1){
	val=ulTaskNotifyTake(pdTRUE,pdMS_TO_TICKS(5));
		if(val){
			cnt++;
			if(cnt==1){
				vTaskResume(Movein_Handle);
				vTaskResume(Moveout_Handle);
				vTaskResume(QR_Handle);
				vTaskResume(Put_Handle);
				Route_FourthGear();
				vTaskDelay(15);
				Route_ThirdGear();
				vTaskDelay(15);				
				Route_SecondGear();
				vTaskDelay(15);
				Route_FirstGear();
				vTaskDelay(15);
				Route_GoLineLow();
				vTaskDelay(90);
				Route_Stop();
				vTaskDelay(250);
				xTaskNotifyGive(Drop_Handle);
				vTaskDelay(2500);			
				xTaskNotifyGive(Forward_Handle);
				
			}
			else if(cnt<=7){
				if(cnt==2){
					vTaskDelete(Drop_Handle);
					vTaskDelete(Recognition_Handle);
					vTaskDelete(Judge_Handle);
					vTaskDelete(Select_Handle);
				}				
				Route_GoLineLow();
				vTaskDelay(25);
				Route_Stop();
				xTaskNotifyGive(Movein_Handle);
				
			}
			vTaskSuspend(NULL);
		}
	}
}
/*
****************************向货站平移*********************************
第一路灰度检测到白线后继续平移一段距离，开启USART2，为扫码数据传输做准备
*/
void Movein_task(void *pvParameters){
	uint16_t val;
	while(1){
		val=ulTaskNotifyTake(pdTRUE,pdMS_TO_TICKS(5));
		if(val){
			while(GREY_1!=0){
				Route_Movein();
			}
			vTaskDelay(30);
			Route_Stop();
			vTaskDelay(70);
			USART2_Start();
			xTaskNotifyGive(QR_Handle);
		}
	}
}
/*
*************************************扫码********************************************
调用QR函数，如果扫到的码数值和上一次扫到的相同或者值为6，那么再次进行扫码确认扫码结果
*/
void QR_task(void *pvParameters){
	TickType_t xLastWakeTime;	
	extern u8 uart_buf[32];
	uint16_t val,Send_QR,past_QR;
	while(1){
		val=ulTaskNotifyTake(pdTRUE,pdMS_TO_TICKS(5));
		if(val){
			Send_QR=QR();
			while(Send_QR==6||Send_QR==past_QR){
				Send_QR=QR();
			}
			past_QR=Send_QR;
			USART2_Stop();
			xQueueSendToBack(xQueueQR,&Send_QR,pdMS_TO_TICKS(5));
			xTaskNotifyGive(Put_Handle);
			vTaskSuspend(QR_Handle);	
		}

		xLastWakeTime = xTaskGetTickCount();
		vTaskDelayUntil(&xLastWakeTime,100);
	}
}
/*
****************************************投球**************************************
如果接收到的扫码器信号为0，那么无需投球直接播报并撤出
如果非0，那么调用put让转盘转到对应位置，调用open开启转盘门，然后close关闭结束投球
*/
void Put_task(void *pvParameters){	
	uint16_t val,Receive_QR,cnt;
	unsigned short Zero_QR;
	while(1){
		val=ulTaskNotifyTake(pdTRUE,pdMS_TO_TICKS(5));
		if(val){
			xQueueReceive(xQueueQR,&Receive_QR,pdMS_TO_TICKS(5));
			if(Receive_QR==0){
				vTaskResume(Speak_Handle);
				Zero_QR=(unsigned short)Receive_QR;
				xQueueSendToBack(xQueueSpeak,&Zero_QR,pdMS_TO_TICKS(5));
				xTaskNotifyGive(Speak_Handle);
				vTaskDelay(350);
			}
			else{
				for(cnt=0;cnt<=4;cnt++){
					if(Receive_QR==position[cnt].index){
						break;
					}
				}
				vTaskResume(Speak_Handle);
				xQueueSendToBack(xQueueSpeak,&position[cnt].index,pdMS_TO_TICKS(5));
				xTaskNotifyGive(Speak_Handle);
				Put(cnt);
				vTaskDelay(100);
				Open();
				vTaskDelay(280);
				Close();			
			}
			xTaskNotifyGive(Moveout_Handle);
		}
	}
}
/*
************************************远离货站平移*******************************************
一直向外平移，直到第七路灰度检测到了白线，判断回到了赛道中
如果判断到第六次移出，那么认为六个货站（包含空货站）均已经投放完毕，则删除掉不需要的子任务
*/
void Moveout_task(void *pvParameters){	
	uint16_t val,cnt;
	while(1){
		val=ulTaskNotifyTake(pdTRUE,pdMS_TO_TICKS(5));
		if(val){
			cnt++;
			while(GREY_7!=0){
				Route_Moveout();
			}	
			Route_Stop();
			vTaskResume(Goline_Handle);
			if(cnt==6){
				UART4_Start();
				UART5_Stop();
				vTaskDelete(TOF_Handle);
				vTaskDelete(Stop_Handle);
				vTaskResume(Wave_Handle);
				vTaskResume(Avoid_Handle);
			}
			xTaskNotifyGive(Forward_Handle);
		}
	}
}
/*
*********************停车后启动**********************
停车完成后，重新启动侧边测距、扫码、巡线和停车的子任务
*/
void Forward_task(void *pvParameters){
	uint16_t val;
	while(1){
		val=ulTaskNotifyTake(pdTRUE,pdMS_TO_TICKS(5));
		if(val){
			vTaskResume(TOF_Handle);
			vTaskResume(Stop_Handle);	
			vTaskResume(QR_Handle);
			vTaskResume(Goline_Handle);
		}
	}

}
/*
**************************避障*****************************
接收到前方测距子任务发来的信号后利用Movein和Moveout进行避障
*/
void Avoid_task(void *pvParameters){
	TickType_t xLastWakeTime;	
	uint16_t val;
	while(1){
		val=ulTaskNotifyTake(pdTRUE,pdMS_TO_TICKS(5));
		if(val){
			Route_Moveout();
			vTaskDelay(200);
			Route_Straight();
			vTaskDelay(250);
			while(GREY_6!=0){
				Route_Movein();
			}
			vTaskResume(GoLineNew_Handle);
			vTaskDelete(Wave_Handle);
			vTaskDelete(Avoid_Handle);
		}
		xLastWakeTime = xTaskGetTickCount();
		vTaskDelayUntil(&xLastWakeTime,20);
	}
}
/*
*******************语音播报********************************
*/
void Speak_task(void *pvParameters){
	TickType_t xLastWakeTime;	
	unsigned short tag;
	uint16_t val;
	while(1){
		val=ulTaskNotifyTake(pdTRUE,pdMS_TO_TICKS(5));
		if(val){
			xQueueReceive(xQueueSpeak,&tag,pdMS_TO_TICKS(5));
			switch(tag){
				case 0:
					SYN_FrameInfo(0,"[v16][m0][t5]此站无邮件");
					break;
				case 1:
					SYN_FrameInfo(0,"[v16][m0][t5]1货站投放成功");
					break;
				case 2:
					SYN_FrameInfo(0,"[v16][m0][t5]2货站投放成功");
					break;
				case 3:
					SYN_FrameInfo(0,"[v16][m0][t5]3货站投放成功");
					break;
				case 4:
					SYN_FrameInfo(0,"[v16][m0][t5]4货站投放成功");
					break;
				case 5:
					SYN_FrameInfo(0,"[v16][m0][t5]5货站投放成功");
					break;	
			}
			vTaskSuspend(NULL);
		}
		xLastWakeTime = xTaskGetTickCount();
		vTaskDelayUntil(&xLastWakeTime,200);
	}	
	
}
/*
************************************二版巡线************************************
在过完跷跷板后，原来的巡线功能过于不能顾及返回出发区，因此在过完跷跷板后使用带有
Gohome功能的巡线子任务
*/
void GoLineNew_task(void *pvParameters){
	while(1)
	{
		if(GREY_1==0){
			xTaskNotifyGive(Gohome_Handle);
			vTaskDelete(NULL);
		}
		else{
			Route_GoLine();
		}
	}
}
/*
******************返回出发区*********************
*/
void Gohome_task(void *pvParameters){
	uint16_t val;
	while(1){
		val=ulTaskNotifyTake(pdTRUE,pdMS_TO_TICKS(5));
		if(val){
			Route_Start();
			vTaskDelay(70);
			Route_Straight();
			vTaskDelay(80);
			Route_Moveout();	
			vTaskDelay(80);
			Route_Stop();
			vTaskSuspendAll();
		}
	}
	
}
/*做测试用子任务*/
void Test_task(void *pvParameters){
	Route_Movein();
}
int main(void)
{
	__init__();
	
	printf("FreeRTOS test\n");
	prvSetupHardware();
	xQueueHC=xQueueCreate(1,sizeof(HC));							//RGB和HSL传输队列
	xQueueIndex=xQueueCreate(1,sizeof(uint16_t));			//颜色对应数字传输队列
	xQueueTOF=xQueueCreate(1,sizeof(uint16_t));				//激光测距传输队列
	xQueueQR=xQueueCreate(1,sizeof(uint16_t));				//二维码测距传输队列
	xQueueSpeak=xQueueCreate(1,sizeof(unsigned short));			//语音播报传输队列
	
	xTaskCreate(RervoReset_task,"ServoReset",1024,NULL,3,NULL);
	xTaskCreate(Start_task,"Start",128,NULL,3,NULL);
	xTaskCreate(Drop_task,"Drop",128,NULL,1,&Drop_Handle);
	xTaskCreate(Recognition_task,"Recognition",256,NULL,1,&Recognition_Handle);
	xTaskCreate(Judge_task,"Judge",128,NULL,1,&Judge_Handle);
	xTaskCreate(Select_task,"Select",128,NULL,1,&Select_Handle);
	xTaskCreate(GoLine_task,"GoLine",128,NULL,1,&Goline_Handle);	
	xTaskCreate(Stop_task,"Stop",128,NULL,1,&Stop_Handle);
	xTaskCreate(Movein_task,"Movein",128,NULL,1,&Movein_Handle);
	xTaskCreate(QR_task,"QR",128,NULL,1,&QR_Handle);
	xTaskCreate(Put_task,"Put",128,NULL,1,&Put_Handle);
	xTaskCreate(Speak_task,"Speak",128,NULL,2,&Speak_Handle);
	xTaskCreate(Moveout_task,"Moveout",128,NULL,1,&Moveout_Handle);	
	xTaskCreate(Forward_task,"Forward",128,NULL,1,&Forward_Handle);
	xTaskCreate(Avoid_task,"Avoid",128,NULL,2,&Avoid_Handle);
	xTaskCreate(TOF_task,"TOF",128,NULL,2,&TOF_Handle);
	xTaskCreate(Wave_task,"Wave",128,NULL,2,&Wave_Handle);
	xTaskCreate(GoLineNew_task,"GoLineNew",128,NULL,1,&GoLineNew_Handle);
	xTaskCreate(Gohome_task,"Gohome",128,NULL,1,&Gohome_Handle);
	
  vTaskStartScheduler();
}

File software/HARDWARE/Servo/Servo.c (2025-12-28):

#include "Servo.h"
#include "stm32f10x.h"
#include "delay.h"

//TIM2 PWM部分初始化 
//PWM输出初始化
//arr：自动重装值
//psc：时钟预分频数

u8 recv_ok = 0;       //接收完成标志
u8 uart_buf[32]={0};  //用于保存串口数据
u8 uart_cnt=0;        //用于定位串口数据的位置

void TIM5_PWM_Init(u16 arr,u16 psc)
{  
	GPIO_InitTypeDef GPIO_InitStructure;
	TIM_TimeBaseInitTypeDef  TIM_TimeBaseStructure;
	TIM_OCInitTypeDef  TIM_OCInitStructure;
	

	RCC_APB1PeriphClockCmd(RCC_APB1Periph_TIM5, ENABLE);	//使能定时器2时钟
 	RCC_APB2PeriphClockCmd(RCC_APB2Periph_GPIOA  | RCC_APB2Periph_AFIO, ENABLE);  //使能GPIO外设和AFIO复用功能模块时钟

	
	
	
   //设置该引脚为输出功能,输出TIM7 CH3、CH4的PWM脉冲波形	GPIOA.2 GPIOA.3
	GPIO_InitStructure.GPIO_Pin =GPIO_Pin_0|GPIO_Pin_1; //TIM7_CH3
	GPIO_InitStructure.GPIO_Mode = GPIO_Mode_AF_PP;  //推挽输出
	GPIO_InitStructure.GPIO_Speed = GPIO_Speed_50MHz;
	GPIO_Init(GPIOA, &GPIO_InitStructure);//初始化GPIO
 
 

   //初始化TIM7
	TIM_TimeBaseStructure.TIM_Period = arr; //设置在下一个更新事件装入活动的自动重装载寄存器周期的值
	TIM_TimeBaseStructure.TIM_Prescaler =psc; //设置用来作为TIMx时钟频率除数的预分频值 
	TIM_TimeBaseStructure.TIM_ClockDivision = 0; //设置时钟分割:TDTS = Tck_tim
	TIM_TimeBaseStructure.TIM_CounterMode = TIM_CounterMode_Up;  //TIM向上计数模式
	TIM_TimeBaseInit(TIM5, &TIM_TimeBaseStructure); //根据TIM_TimeBaseInitStruct中指定的参数初始化TIMx的时间基数单位
	
	//初始化TIM7 Channel2 PWM模式	 
	TIM_OCInitStructure.TIM_OCMode = TIM_OCMode_PWM1; //选择定时器模式:TIM脉冲宽度调制模式2
 	TIM_OCInitStructure.TIM_OutputState = TIM_OutputState_Enable; //比较输出使能
	TIM_OCInitStructure.TIM_OCPolarity = TIM_OCPolarity_High; //输出极性:TIM输出比较极性高
	
	TIM_OC1Init(TIM5, &TIM_OCInitStructure);        //根据T指定的参数初始化外设TIM7 OC2
  TIM_OC1PreloadConfig(TIM5, TIM_OCPreload_Enable);// 使能预装载寄存�
	
	TIM_OC2Init(TIM5, &TIM_OCInitStructure);        //根据T指定的参数初始化外设TIM7 OC2
  TIM_OC2PreloadConfig(TIM5, TIM_OCPreload_Enable);// 使能预装载寄存器
	
	TIM_Cmd(TIM5, ENABLE);  //使能TIM7

}


////TIM2 PWM部分初始化 
////PWM输出初始化
////arr：自动重装值
////psc：时钟预分频数
void TIM2_PWM_Init(u16 arr,u16 psc)
{  
	GPIO_InitTypeDef GPIO_InitStructure;
	TIM_TimeBaseInitTypeDef  TIM_TimeBaseStructure;
	TIM_OCInitTypeDef  TIM_OCInitStructure;
	
	RCC_APB1PeriphClockCmd(RCC_APB1Periph_TIM2, ENABLE);	//使能定时器2时钟
 	RCC_APB2PeriphClockCmd(RCC_APB2Periph_GPIOA|RCC_APB2Periph_GPIOB| RCC_APB2Periph_AFIO, ENABLE);  //使能GPIO外设和AFIO复用功能模块时钟
	GPIO_PinRemapConfig(GPIO_FullRemap_TIM2 , ENABLE); //Timer2重映射  TIM2_CH2->PB5  

   //设置该引脚为输出功能,输出TIM7 CH3、CH4的PWM脉冲波形	GPIOA.2 GPIOA.3
	GPIO_InitStructure.GPIO_Pin =GPIO_Pin_15; //TIM7_CH3
	GPIO_InitStructure.GPIO_Mode = GPIO_Mode_AF_PP;  //推挽输出
	GPIO_InitStructure.GPIO_Speed = GPIO_Speed_50MHz;
	GPIO_Init(GPIOA, &GPIO_InitStructure);//初始化GPIO	
	
   //设置该引脚为输出功能,输出TIM7 CH3、CH4的PWM脉冲波形	GPIOA.2 GPIOA.3
	GPIO_InitStructure.GPIO_Pin =GPIO_Pin_3|GPIO_Pin_10|GPIO_Pin_11; //TIM7_CH3
	GPIO_InitStructure.GPIO_Mode = GPIO_Mode_AF_PP;  //推挽输出
	GPIO_InitStructure.GPIO_Speed = GPIO_Speed_50MHz;
	GPIO_Init(GPIOB, &GPIO_InitStructure);//初始化GPIO

	
   //初始化TIM2
	TIM_TimeBaseStructure.TIM_Period = arr; //设置在下一个更新事件装入活动的自动重装载寄存器周期的值
	TIM_TimeBaseStructure.TIM_Prescaler =psc; //设置用来作为TIMx时钟频率除数的预分频值 
	TIM_TimeBaseStructure.TIM_ClockDivision = 0; //设置时钟分割:TDTS = Tck_tim
	TIM_TimeBaseStructure.TIM_CounterMode = TIM_CounterMode_Up;  //TIM向上计数模式
	TIM_TimeBaseInit(TIM2, &TIM_TimeBaseStructure); //根据TIM_TimeBaseInitStruct中指定的参数初始化TIMx的时间基数单位
	
	//初始化TIM7 Channel2 PWM模式	 
	TIM_OCInitStructure.TIM_OCMode = TIM_OCMode_PWM1; //选择定时器模式:TIM脉冲宽度调制模式2
 	TIM_OCInitStructure.TIM_OutputState = TIM_OutputState_Enable; //比较输出使能
	TIM_OCInitStructure.TIM_OCPolarity = TIM_OCPolarity_High; //输出极性:TIM输出比较极性高
	
	
	TIM_OC1Init(TIM2, &TIM_OCInitStructure);        //根据T指定的参数初始化外设TIM7 OC1
  TIM_OC1PreloadConfig(TIM2, TIM_OCPreload_Enable);// 使能预装载寄存器
	
	TIM_OC2Init(TIM2, &TIM_OCInitStructure);        //根据T指定的参数初始化外设TIM7 OC2
  TIM_OC2PreloadConfig(TIM2, TIM_OCPreload_Enable);// 使能预装载寄存器

	TIM_OC3Init(TIM2, &TIM_OCInitStructure);  //根据T指定的参数初始化外设TIM7 OC3
  TIM_OC3PreloadConfig(TIM2, TIM_OCPreload_Enable);// 使能预装载寄存器
	
  TIM_OC4Init(TIM2, &TIM_OCInitStructure);        //根据T指定的参数初始化外设TIM7 O4   
	TIM_OC4PreloadConfig(TIM2, TIM_OCPreload_Enable);// 使能预装载寄存器
	
	TIM_Cmd(TIM2, ENABLE);  //使能TIM7

}	
/*
*********************扫码器*********************
利用strstr函数找到返回的字符型数值，再将数值赋值给Number
*/
uint16_t QR(void){
	uint16_t Number;
	if(recv_ok==1)  //接收完成
	{			
		if(strstr((char*)uart_buf,"0")) Number=0;

		if(strstr((char*)uart_buf,"1"))	Number=1;

		if(strstr((char*)uart_buf,"2"))	Number=2;

		if(strstr((char*)uart_buf,"3"))	Number=3;

		if(strstr((char*)uart_buf,"4"))	Number=4;

		if(strstr((char*)uart_buf,"5"))	Number=5;

		uart_cnt = 0;        //最后清零，重新计数
		recv_ok = 0;         //接收完成标志置0
		return Number;
	}
	else{
		return 6;
	}

}
/*
***********************************投球相关函数****************************************
Put：转盘转到对应位置，1560为安装测试后的初始位置，需自行调整，建议后续使用时进行宏定义
Open、Close：开关门，1500和500均为安装测试后位置，需自行调整
*/
void Put(uint16_t Number){
	if(Number<=2){
		TIM_SetCompare2(TIM2,1560+Number*400);
	}
	else{
		TIM_SetCompare2(TIM2,750+(Number-3)*400);
	}
}
void Open(void){
	TIM_SetCompare4(TIM2,1500);	
}
void Close(void){
	TIM_SetCompare4(TIM2,500);	
}

void USART2_Start(void)
{
	USART_ITConfig(USART2, USART_IT_RXNE, ENABLE);								
}
void USART2_Stop(void)
{
	USART_ITConfig(USART2, USART_IT_RXNE, DISABLE);
}

void USART2_IRQHandler(void)      //UASRT2中断服务程序
{
 uint8_t d;

 //检测标志位
 if(USART_GetITStatus(USART2, USART_IT_RXNE)!=RESET)
 {
  //接受数据
  d = USART_ReceiveData(USART2);
     //将接受到的数据依次保存到数组里
  uart_buf[uart_cnt++] = d;  
  //GM65模块发完一组数据后会自动发送一个回车符，所以通过检测是否接受到回车来判断数据是否接受完成
  if(d == 0x0D) 
  {
   recv_ok = 1;  //接受完成
  }

  USART_ClearITPendingBit(USART2,USART_IT_RXNE); //清空标志位
 } 
}

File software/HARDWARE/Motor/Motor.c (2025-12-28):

#include "Motor.h"
#include "stm32f10x.h"

void Motor_Configure(void){
	GPIO_InitTypeDef GPIO_InitStructure;
	TIM_TimeBaseInitTypeDef  TIM_TimeBaseStructure;
	TIM_OCInitTypeDef  TIM_OCInitStructure;
	
	RCC_APB1PeriphClockCmd(RCC_APB1Periph_TIM4|RCC_APB1Periph_TIM3, ENABLE); 
	RCC_APB2PeriphClockCmd(RCC_APB2Periph_GPIOB|RCC_APB2Periph_AFIO|RCC_APB2Periph_GPIOA,ENABLE);
	TIM_DeInit(TIM4);
	TIM_DeInit(TIM3);
	
	GPIO_InitStructure.GPIO_Pin = GPIO_Pin_0|GPIO_Pin_1|GPIO_Pin_6 | GPIO_Pin_7| GPIO_Pin_8| GPIO_Pin_9;
	GPIO_InitStructure.GPIO_Mode = GPIO_Mode_AF_PP;  //复用推挽输出
	GPIO_InitStructure.GPIO_Speed = GPIO_Speed_50MHz;
	GPIO_Init(GPIOB, &GPIO_InitStructure);//初始化GPIO
	
	GPIO_InitStructure.GPIO_Pin =GPIO_Pin_6 | GPIO_Pin_7;	
	GPIO_Init(GPIOA, &GPIO_InitStructure);//初始化GPIO
	
	TIM_TimeBaseStructure.TIM_Period = 1010-1;
  TIM_TimeBaseStructure.TIM_Prescaler = 6-1;  //17 4K   19 3.6K  533 135HZ
  TIM_TimeBaseStructure.TIM_ClockDivision = 0;
  TIM_TimeBaseStructure.TIM_CounterMode = TIM_CounterMode_Up;
  TIM_TimeBaseInit(TIM4, &TIM_TimeBaseStructure);
	TIM_TimeBaseInit(TIM3, &TIM_TimeBaseStructure);
	
	TIM_OCInitStructure.TIM_OCMode = TIM_OCMode_PWM1;
  TIM_OCInitStructure.TIM_OutputState = TIM_OutputState_Enable;
  TIM_OCInitStructure.TIM_OCPolarity = TIM_OCPolarity_High;
	
  TIM_OC1Init(TIM4, &TIM_OCInitStructure); 
  TIM_OC1PreloadConfig(TIM4, TIM_OCPreload_Enable);//使能的预装载寄存器

  TIM_OC2Init(TIM4, &TIM_OCInitStructure); 
  TIM_OC2PreloadConfig(TIM4, TIM_OCPreload_Enable);//使能的预装载寄存器

  TIM_OC3Init(TIM4, &TIM_OCInitStructure); 
  TIM_OC3PreloadConfig(TIM4, TIM_OCPreload_Enable);//使能的预装载寄存器

  TIM_OC4Init(TIM4, &TIM_OCInitStructure); 
  TIM_OC4PreloadConfig(TIM4, TIM_OCPreload_Enable);//使能的预装载寄存器

/**************************************************************************/
	
  TIM_OC1Init(TIM3, &TIM_OCInitStructure); 
  TIM_OC1PreloadConfig(TIM3, TIM_OCPreload_Enable);//使能的预装载寄存器
	
  TIM_OC2Init(TIM3, &TIM_OCInitStructure); 
  TIM_OC2PreloadConfig(TIM3, TIM_OCPreload_Enable);//使能的预装载寄存器
	
  TIM_OC3Init(TIM3, &TIM_OCInitStructure); 
  TIM_OC3PreloadConfig(TIM3, TIM_OCPreload_Enable);//使能的预装载寄存器
	
  TIM_OC4Init(TIM3, &TIM_OCInitStructure); 
  TIM_OC4PreloadConfig(TIM3, TIM_OCPreload_Enable);//使能的预装载寄存器
    
  TIM_ARRPreloadConfig(TIM4, ENABLE);	//使能定时器4
	TIM_ARRPreloadConfig(TIM3, ENABLE);	//使能定时器3
  TIM_Cmd(TIM4, ENABLE);
	TIM_Cmd(TIM3, ENABLE);

}
/*
port选择对应驱动端口，speed调整端口输出的PWM波占空比以调整速度
speed不得大于950，否则驱动将会损坏！！！！！！！
*/
void Motor(u8 port, s16 speed)
{
	if(speed >= 0)
	{
		if(speed>1000) speed=1000;
		switch(port)
		{
			case 1:  
				TIM4->CCR1 =  speed;
				TIM4->CCR2 =  0;   
				break;
			case 2:
				TIM4->CCR3 =  speed;
				TIM4->CCR4 =  0; 
				break;
			case 3:
				TIM3->CCR1 =  speed;
				TIM3->CCR2 =  0; 
				break;
			case 4:
				TIM3->CCR3 =  speed;
				TIM3->CCR4 =  0; 
				break;      
		}
	} 
	else 
	{
		if(speed<-1000) speed=-1000;
		switch(port)
		{
			case 1:
				TIM4->CCR1 =  0;
				TIM4->CCR2 =  -speed;			
				break;
			case 2:
				TIM4->CCR3 =  0;
				TIM4->CCR4 =  -speed; 
				break;
			case 3:
				TIM3->CCR1 =  0;
				TIM3->CCR2 =  -speed; 
				break;
			case 4:
				TIM3->CCR3 =  0;
				TIM3->CCR4 =  -speed; 
				break;   
		}
	}   
}
